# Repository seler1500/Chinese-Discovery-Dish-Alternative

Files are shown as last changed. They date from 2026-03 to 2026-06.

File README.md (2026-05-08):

# Chinese Discovery Dish Alternative
A cheaper, portable dish antenna for general weather satellite reception.



## Getting the dish
Search "LTE MIMO Dish antenna" or "LTE Dish antenna" on AliExpress and you are likely to find it in the top results. You can also try negotiating with seller to buy the dish alone for a lower price without the mount and the feed, as you would need a different feed for weather satellite reception anyway. The price fluctuates often, so it's worth waiting for a sale or discount.

## Dimensions
The four reflector plates are made out of powder coated aluminum, fit in a regular backpack, and assemble into a 60cm prime focus dish.

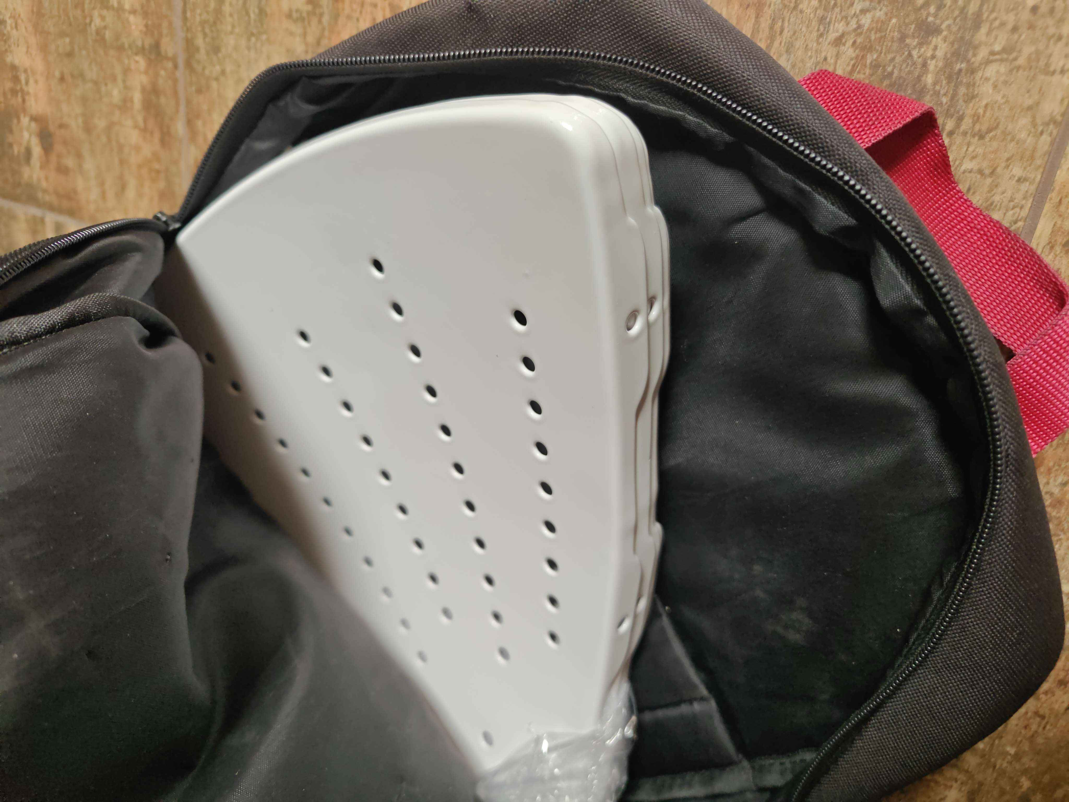
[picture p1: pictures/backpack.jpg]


Standard metric hardware is supplied with the dish. M5 for assembling the plates, M6 for attaching the feed/feedarm adapter. I ended up using the supplied bolts, but replaced the nuts with stainless wing nuts to simplify the assembly. Four M6 and eight M5 wing nuts are needed. For attaching the backfire helix, i used three M4x16 nylon bolts with nylon nuts. 

## The feed and feedarm
You likely won't need the original feed. It's very wideband, linearly polarized - and doesn't even perform well on linear signals. I highly recommend Digitelektro's backfire helix:
https://github.com/Digitelektro/BackfireHelix  
For the feedarm, I'm using a 20 mm aluminum pipe with two printed adapters which are provided in "3d models" directory. I also recommend cutting a notch in the pipe, to prevent damage to the coax when the dish is dropped. 20 mm PVC pipe can be used as well.

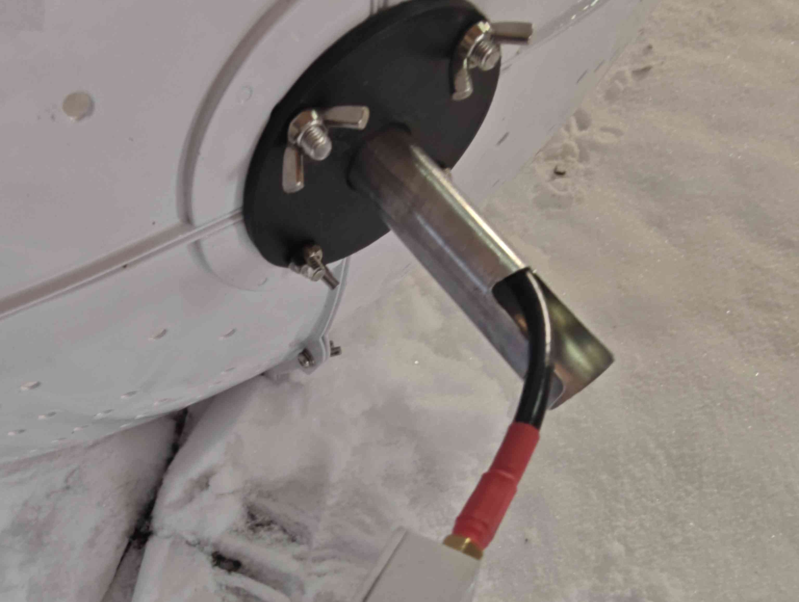
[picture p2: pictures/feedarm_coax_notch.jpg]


The backfire helix side adapter is Aweeri's [***backfire_helix_compact_adapter_for_discovery_dish.STL***](https://github.com/Digitelektro/BackfireHelix/blob/main/stl/backfire_helix_compact_adapter_for_discovery_dish.STL), I just added slots for M4 nuts and removed one bolt hole.  
The backfire helix requires tuning the S11 return loss/SWR to perform well which increases the difficulty. VNA and some tuning knowledge are required. Here is how I do it - but do keep in mind that there are another ways!

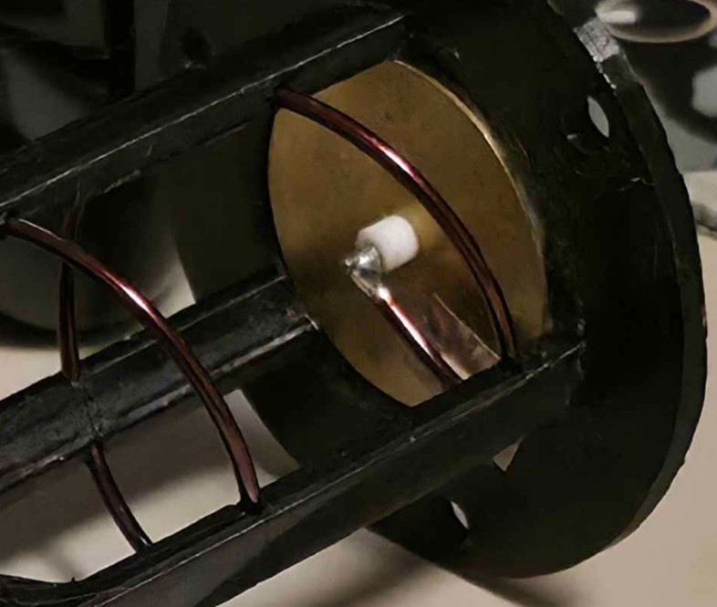
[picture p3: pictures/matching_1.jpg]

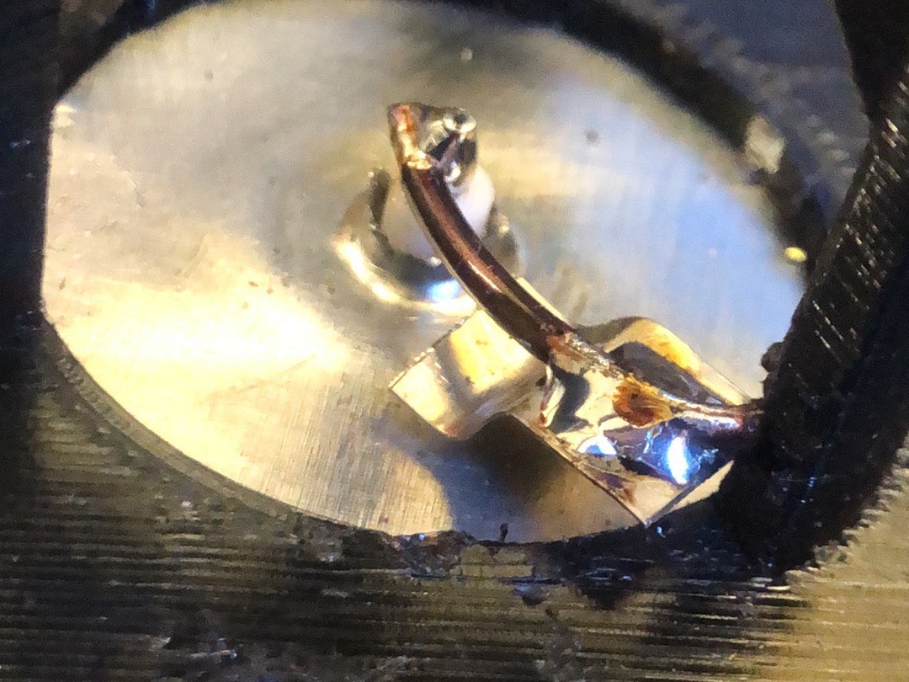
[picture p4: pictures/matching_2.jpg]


When tuning using a simple matching strip, two rough rules are worth acknowledging:  
**Distance between the matching strip and the feedpoint affects the center frequency**  
**Distance between the matching strip and the director affects the S11 Return Loss/SWR**  

#### The elephant in the room (connecting LNAs to the feed)
I opted to connect the LNA to the feed with a short coax. To make it easier, I used a female SMA on the feed. This of course sacrifices some signal strength, as we are adding insertion loss between feed and LNA and possibly some noise trough coax shield. However, I think it's more convinient than having the LNA built-in to the feedarm, and also ensures the LNA enclosure does not affect the radiation pattern.

## Dish assembly
I recommend assembling the dish on a flat, level surface. Start with connecting all plates together with bolts without fully tightening them. Place the dish reflector-side down on a flat surface, and now gradually tighten the bolts. Finally, attach coax to your feed and mount the feedarm and the helix itself.

## Focal point adjustments
To get the best performance, I recommend adjusting the focal point on a test signal, like Elektro L2/L3/L4 for L-band, or SBIRS-GEO for S-band.
SatDump software is commonly used for weather satellite reception, and it has the required pipelines (at least for L-band) to live decode the signal for real time SNR feedback.
For L-Band just use Elektro-L and the GGAK pipeline, adjust the focal lenght while watching the SNR. Keep in mind that GGAK pipeline is notoriously "fiddly" to get a lock, sometimes you'll have to tick the SDR frequency a couple kHz up or down to get a lock. If you don't have Elektro-L LOS, Arktika M2 also transmits GGAK on 1703 MHz, and there's a pipeline for it as well, named accordingly. Keep in mind that Arktika M1 does not transmit GGAK at all, and M2 transmits only at certain altitudes; usually > 30000 km.
For S-band it's a bit trickier; you'll have to use advanced mode and make temporary changes to Metop AHRPT pipeline (modulation to oqpsk, symbol rate to 2500000):

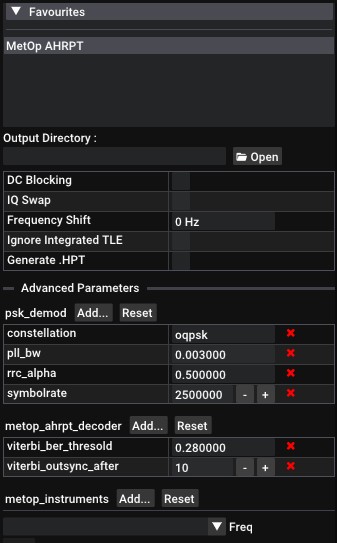
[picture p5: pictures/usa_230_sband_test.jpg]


If you don't want to change the settings every time you need to test something, I have attached a SatDump pipeline for this satellite. You can copy it to `satdump/resources/pipelines` directory if you'd like to use it.  
Assemble your S-Band setup, set the frequency to 2262.5 MHz, start the pipeline and point your dish at one of SBIRS-GEO satellites. All of them use the same frequency and modulation. Once you get a SNR readout, you can start adjusting the focal point for best SNR.
If your SDR has a DC spike, offset tuning and DC Blocking are advised.

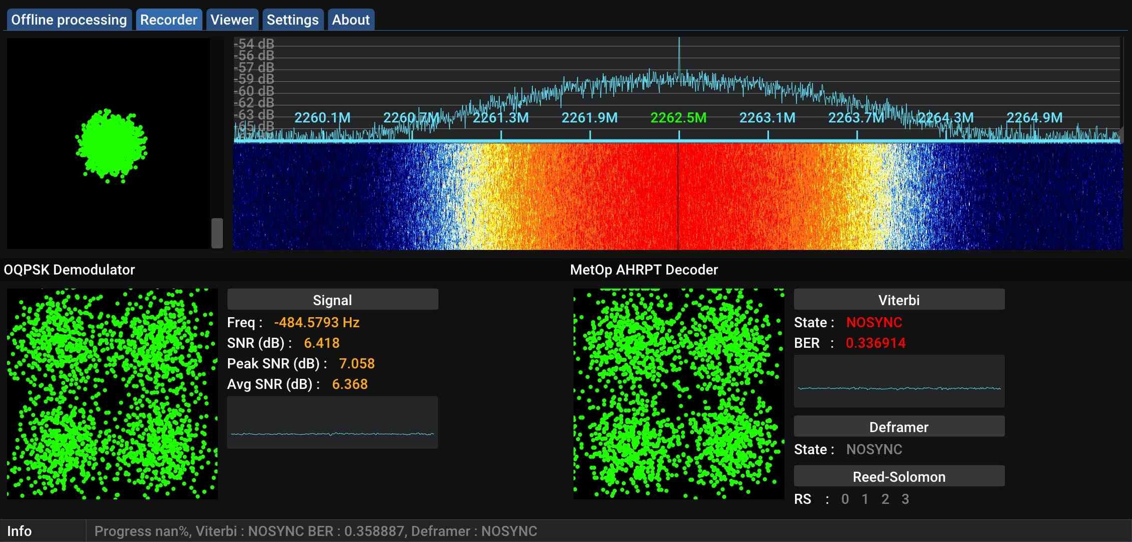
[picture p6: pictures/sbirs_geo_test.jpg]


## Weather satellite benchmarks

### Meteor M2-3, M2-4

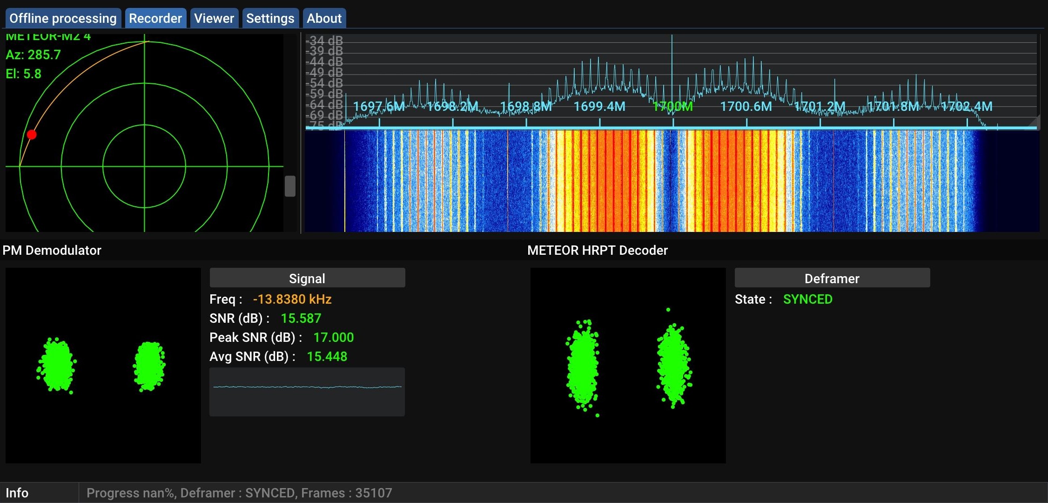
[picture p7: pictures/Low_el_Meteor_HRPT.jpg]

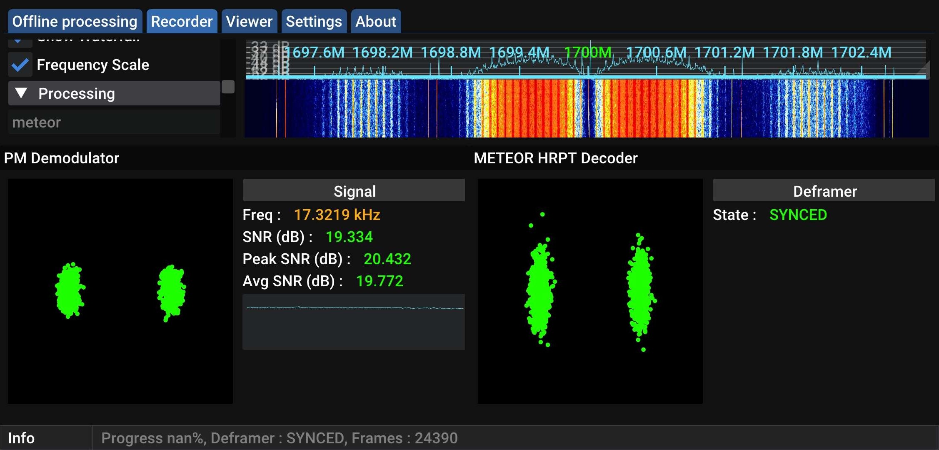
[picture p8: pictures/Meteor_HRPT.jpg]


### Metop B/C
Keep in mind that Metop B has intermittent modulator issues, which causes a distorted constellation and lower SNR.

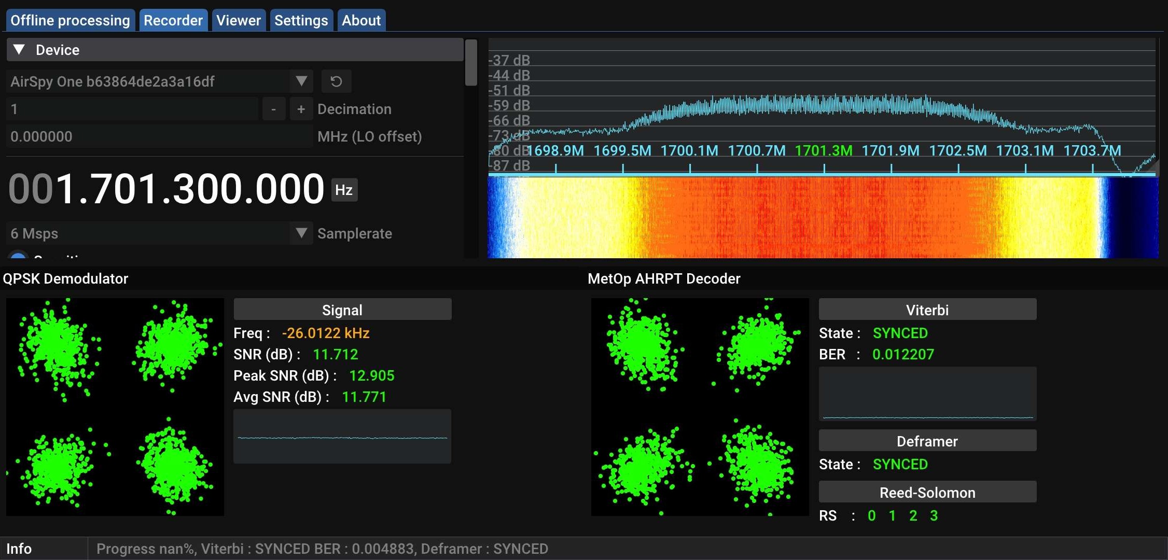
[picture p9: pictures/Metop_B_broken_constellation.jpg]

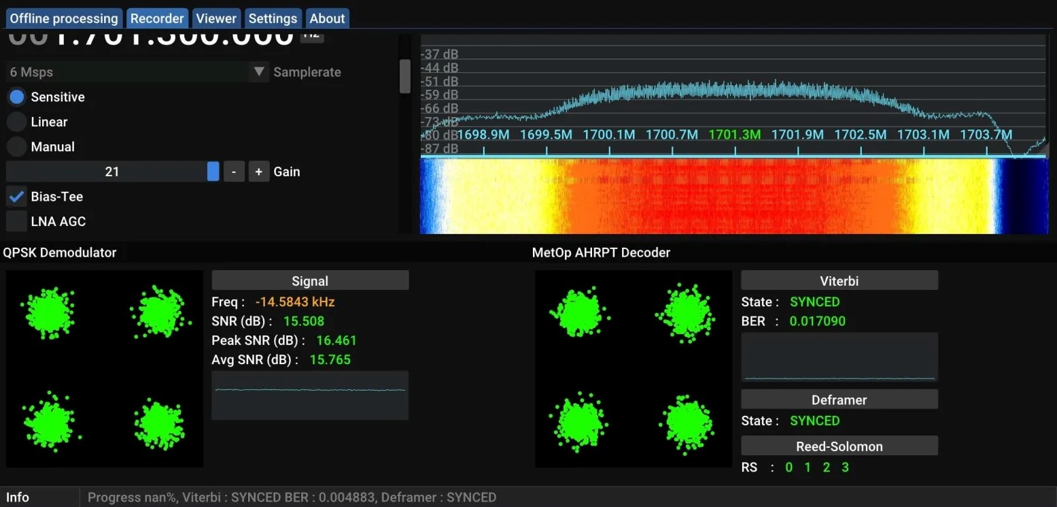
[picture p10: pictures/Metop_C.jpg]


### Elektro L2

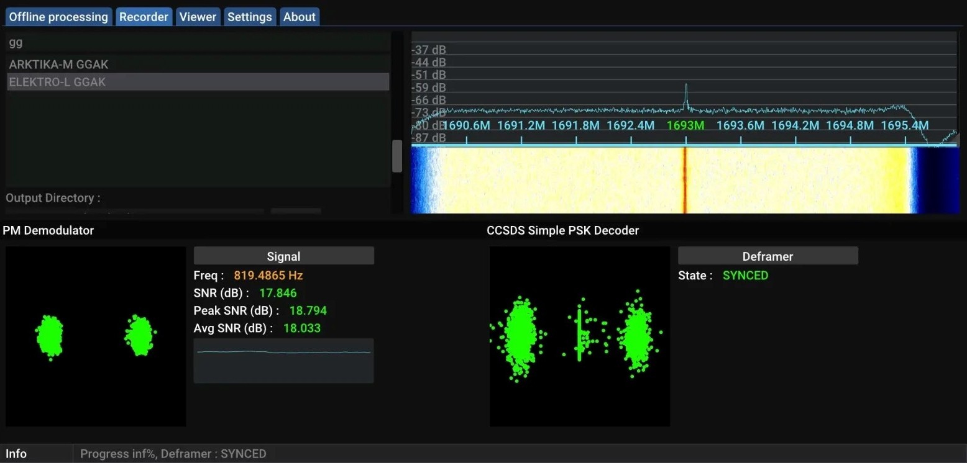
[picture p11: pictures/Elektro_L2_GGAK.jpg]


### Arktika M2 

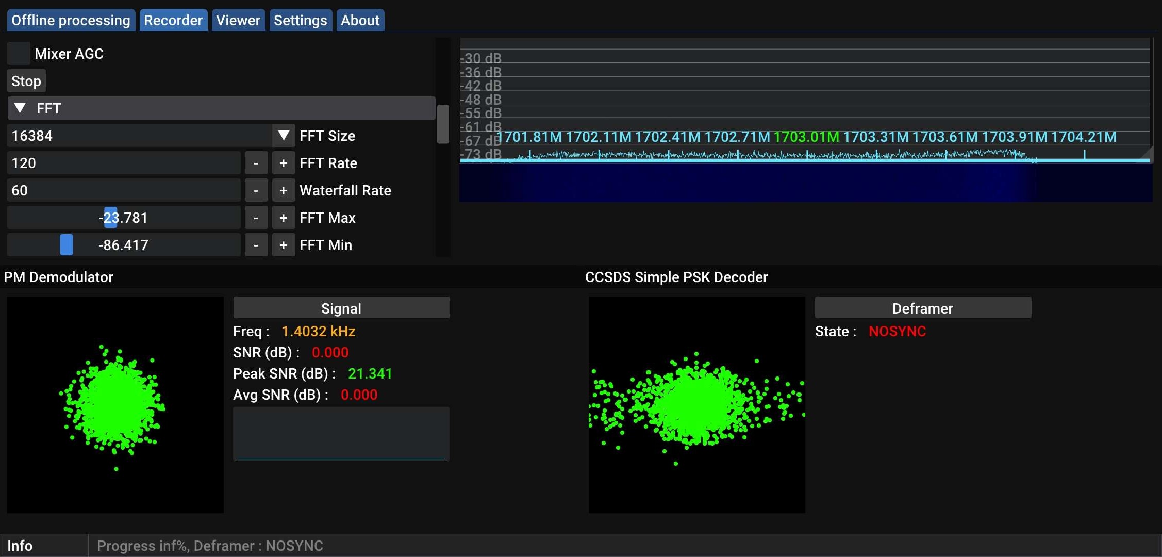
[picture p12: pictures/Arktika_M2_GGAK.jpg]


### Proba 2

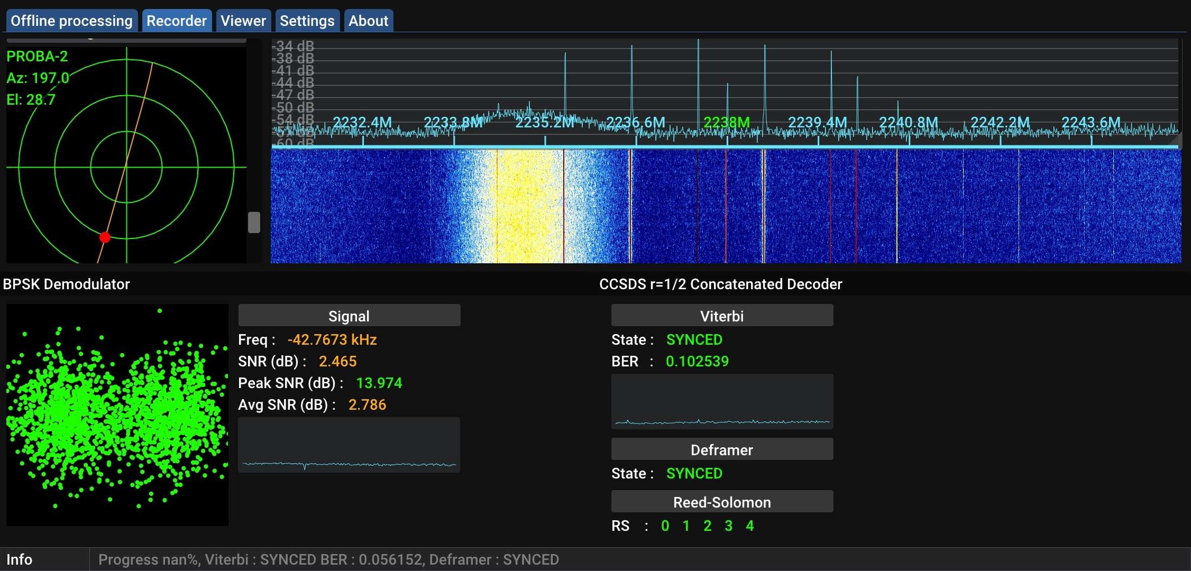
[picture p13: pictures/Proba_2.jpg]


### DMSP F17

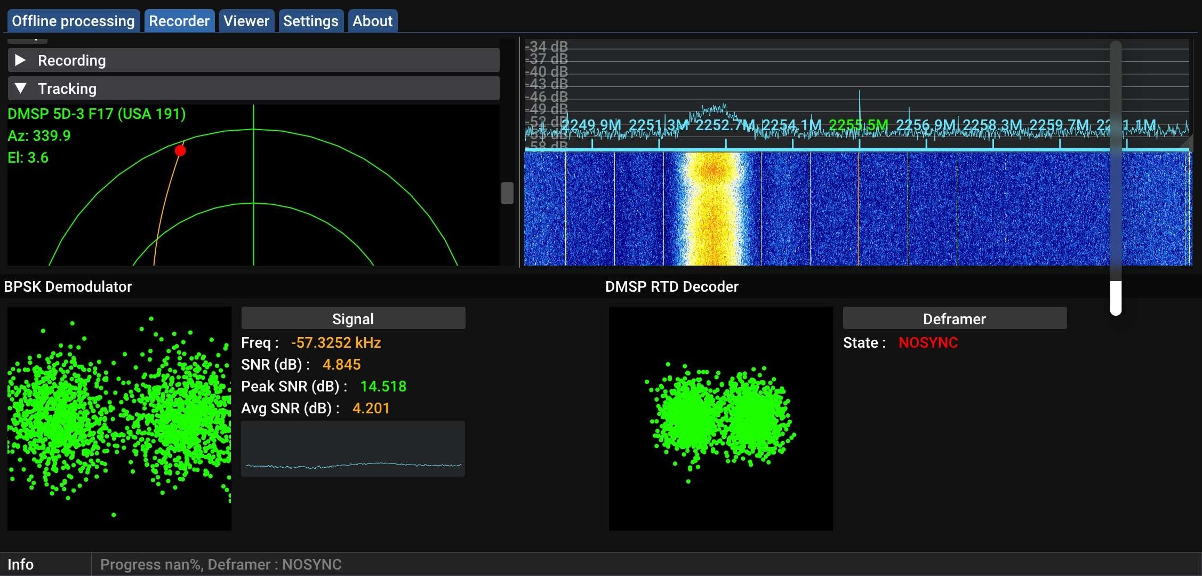
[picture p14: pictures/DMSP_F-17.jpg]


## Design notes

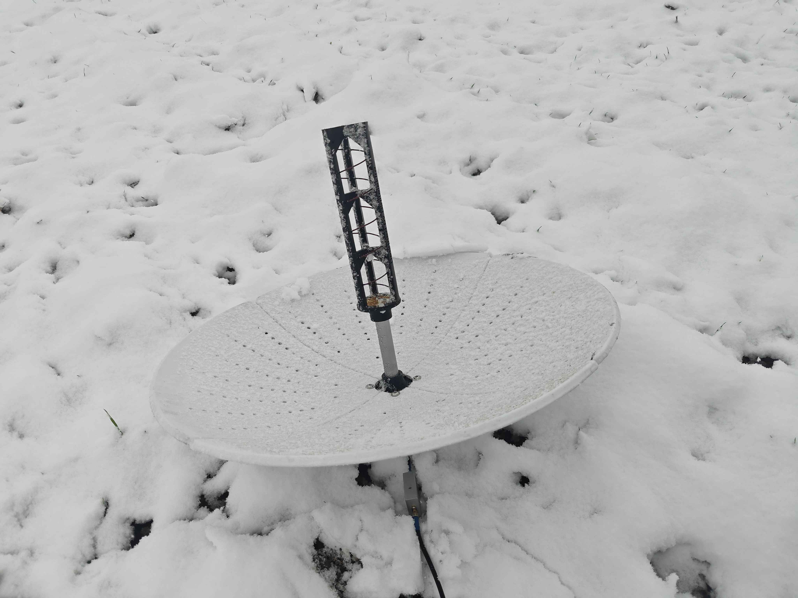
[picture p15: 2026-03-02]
pictures/l-band_snow.jpg

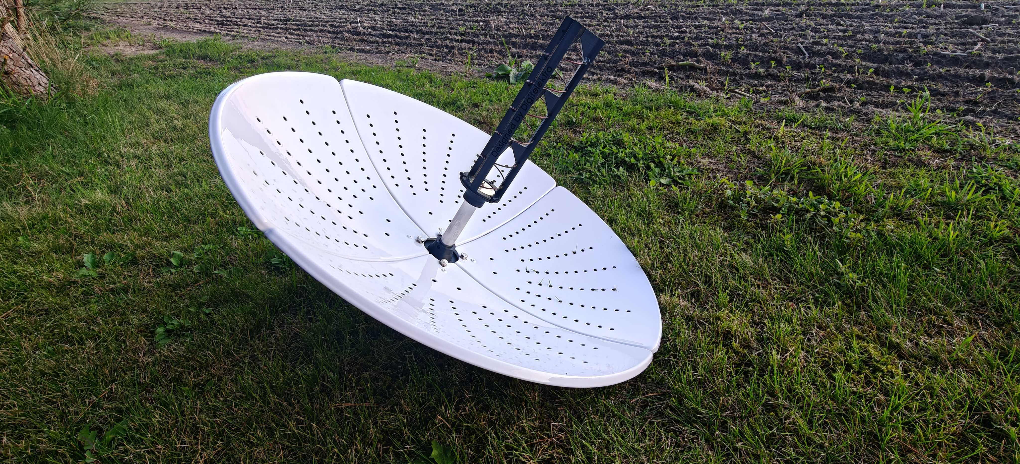
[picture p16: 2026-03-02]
pictures/L-band.jpg

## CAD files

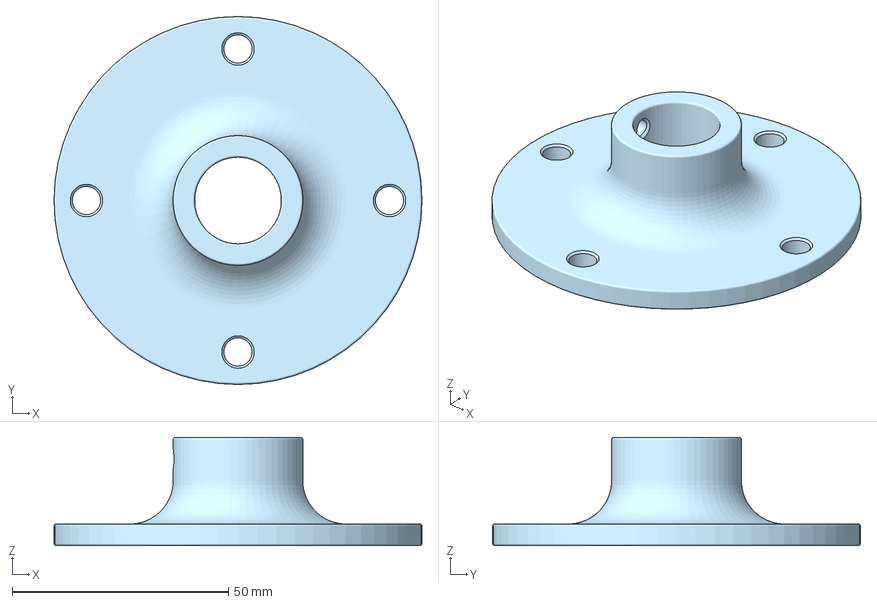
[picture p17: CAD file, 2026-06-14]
3d models/feedarm_mount_v3.3mf
85.0 x 85.0 x 25.0 mm

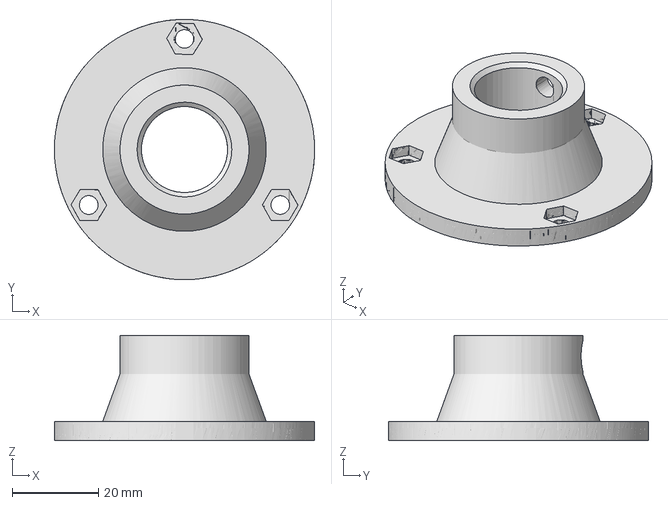
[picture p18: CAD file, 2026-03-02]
3d models/backfire_helix_compact_adapter_for_discovery_dish_improved.3mf
60.5 x 60.4 x 25.9 mm

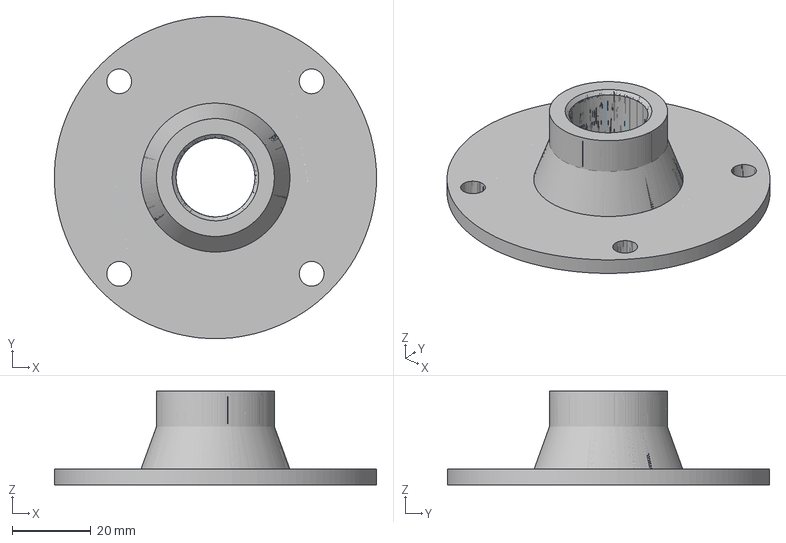
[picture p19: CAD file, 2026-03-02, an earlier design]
3d models/feedarm_mount_v2.3mf
82.0 x 82.0 x 23.9 mm
